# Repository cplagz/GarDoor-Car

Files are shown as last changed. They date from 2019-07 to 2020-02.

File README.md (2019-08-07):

# GarDoor-Car:
Version: 2.00R

## ESP8266 MQTT Garage Door Opener, Garage Door and Car Sensor, and Temperature Monitor using Home Assistant/Blynk
This project allows you to control (open/close) a "dumb" garage door opener for a garage door and independently reports the garage door status (open/closed) and presence of a car in the garage via MQTT and Blynk. In addition you can monitor the Temperature and Humidity within your garage over MQTT as well. This project requires two ultrasonic sensors: one pointed at the garage door, and the other pointed at the normal location of the car. This allows the presence of the car to be detected whether the garage door is open or closed.  

The code covered in this repository utilises Home Assistant's [MQTT Cover Component](https://www.home-assistant.io/components/cover.mqtt/), [MQTT Binary Sensor Component](https://www.home-assistant.io/components/binary_sensor.mqtt/), and [MQTT Sensor Component](https://www.home-assistant.io/components/sensor.mqtt/). There is an example configuration in this repository. GarDoor will respond to HA's open and close commands and reports door/car status to keep HA's GUI in sync with the door and car state. GarDoor should also be controllable via any home automation software that can work with MQTT.  

GarDoor can also be used with the Blynk app (iOS or Android). If you enable this feature, you can monitor the garage door/car status as well as open/close the door with the app. You can also choose to be notified of garage door events on your phone. 

GarDoor requires both hardware and software components. It requires an ESP8266 microcontroller with sensors and a relay. If you select the appropriate parts, you can build a GarDoor-Car device with no soldering! The software component is found in this repo. 

The code is based on DotNetDann's ESP-MQTT-GarageDoorSensor project (thanks Daniel) (which took inspiration from GarHAge and OpenGarage) with added additional features. Parts of the documentation is based on GarHAge documentation (thanks Mark).   

### Supported Features Include
- Reports status of the garage door
- Reports presence of a car in the garage whether the door is open or closed
- Reports ultrasonic sensors distance readings
- Reports information about the ESP8266
- Reports information on temperature and humidity
- Ability to select Celius or Fahrenheit for temperature
- Web page for status of the garage door, car presence, and temperature/humidity
- Ability to use the Blynk App (iOS or Android) to open/close the garage door and monitor door/car status
- Ability to receive Blynk notifications when garage door is opened/closed and when door is left open for more than 15 minutes
- Events and status sent via MQTT
- MQTT commands to toggle relay to open/close the garage door
- Ability to select an Active High or Active Low relay
- Over-the-Air (OTA) Upload from the ArduinoIDE!

### How GarDoor-Car Operates

GarDoor-Car subscribes to a configurable MQTT topic for the garage door (by default, gardoor/1/action).

When the OPEN payload is received on this topic, GarDoor-Car momentarily activates the relay connected to the garage door opener to cause the door to open.

When the CLOSE payload is received on this topic, GarDoor-Car momentarily activates the relay connected to the garage door opener to cause the door to close. By default, GarDoor-Car is configured to activate the same relay for the OPEN and CLOSE payloads, as most (if not all) garage door openers operate manually by momentarily closing the same circuit to both open and close.

When the STATE payload is received on this topic, GarDoor-Car publishes the status of the garage door (open or closed) to the topic gardoor/1/status and the occupied status of the car (true or false) to the topic gardoor/2/status. The distance measurements for the door and car sensors are also included in these messages. These messages are published with the "retain" flag set. To ensure that HA displays up-to-date garage door and car status after a HA restart, it is recommended that you create an automation in Home Assistant that publishes the STATE payload via MQTT on HA start. An example is provided in the Home Assistant Configuration section of this documentation.

When the state of the garage door changes (either because GarDoor-Car (via HA/MQTT or Blynk app) has triggered the door to open or close, or because the door has been opened or closed via a remote, pushbutton switch, key switch, or manually), GarDoor-Car publishes the status (open or closed) and sensor distance measurement of the garage door to gardoor/door/1/status. These messages are published with the "retain" flag set.

When the occupied state of the car changes because the car leaves or enters the garage, GarDoor-Car publishes the occupied status (true or false) and sensor distance measurement of the car to gardoor/2/status. These messages are published with the "retain" flag set.

GarDoor-Car also publishes (topic gardoor/availability) a "birth" message on connection to your MQTT broker, and a "last-will-and-testament" message on disconnection from the broker, so that your home automation software can respond appropriately to GarDoor-Car being online or offline.

GarDoor-Car also publishes to your MQTT broker on topic gardoor/blynkavailability (only if GarDoor-Car is already online; if GarDoor-Car goes offline first, then an automation in your home automation software is required to update the status on the gardoor/blynkavailability topic) a message when GarDoor-Car connects or disconnects from the Blynk server, so that your home automation software can respond appropriately to the GarDoor-Car Blynk connection being online or offline.

GarDoor-Car publishes data about the ESP8266 (topic gardoor/ESPtoMQTT) and temperature/humidity (topics gardoor/temperature and gardoor/humidity) to your MQTT broker.

GarDoor-Car can also connect (if enabled by the user) to a Blynk server. This enables door and car status updates, as well as the door sensor distance measurement to be published to a Blynk server/app. GarDoor-Car can also receieve button requests from the Blynk server/app, which causes GarDoor-Car to momentarily activate the relay connected to the garage door opener to cause the door to open or close. This feature gives a user the ability to press a button in the Blynk app to control the garage door. Notifications can also be published to the Blynk server/app when the garage door open/closes or is left open too long. 

### Hardware Parts List
- [NodeMCU](https://www.aliexpress.com/item/32665100123.html) or other ESP8266-based microcontroller 
- [2 x HC-SR04P Ultrasonic Sensors](https://www.aliexpress.com/item/32711959780.html) May also use HC-SR04 model
- [5V 1 Channel Relay Board](https://www.gearbest.com/relays/pp_226384.html) Active-High or Active-Low supported
- [DHT22 module](https://www.aliexpress.com/item/32899808141.html) (optional)  
- Electrical cable (two-conductor) to connect the relay to your garage door opener 
- Power source for NodeMCU: MicroUSB cable with USB 2.1A power adapter or 5V power supply  
- Male-to-female (and male-to-male if you use HC-SR04 model ultrasonic sensors and need to connect four components to 5v power using the breadboard power rails) breadboard jumper wires (Dupont)
- Breadboard 400 tie-point or larger
- Project box or case (optional)

#### Detailed Hardware

#### 1. ESP8266-based microcontroller
I recommend the NodeMCU as GarDoor-Car was developed and is tested on it. Its advantages are:

- it comes with header pins already soldered so that it can plug directly into a solderless breadboard;
- its VIN (or VU on the LoLin NodeMCU v3 variant) port can power the 5v relay module and DHT22 sensor;
- it can be powered and programmed via MicroUSB;
- it has Reset and Flash buttons, making programming easy.

This guide is written specifically for the NodeMCU. But, GarDoor-Car should also work with the Adafruit HUZZAH, Wemos D1, or similar, though you may need to adjust the GPIO ports used by the sketch to match the ESP8266 ports that your microcontroller makes available.

#### 2. Single 5v relay module
A single 5v relay module makes setup easy: just plug jumper wires from the module's VCC, S, and GND pins to the NodeMCU. Because the relay module is powered by 5v, its inputs can be triggered by the NodeMCU's GPIOs.

GarDoor-Car will work with relay modules that are active-high or active-low; if using an active-low relay, be sure to set the relevant configuration parameter in auth.h, described below, and test thoroughly to be sure that your garage door opener(s) are not inadvertently triggered after a momentary power-loss.

#### 3. Two Ultrasonic Sensors (model HC-SR04P recommended)
GarDoor-Car will work with either the HC-SR04 or HC-SR04P model. The HC-SR04P can use 3.3v or 5v power, while the HC-SR04 requires 5v power. When using the HC-SR04P model (as the wiring diagram below assumes), the maximum distance of the sensor is reduced slightly when using 3.3v power. For the purposes of this project, this shouldn't affect the results of the GarDoor-Car. Thus either model can be used, but it is recommended that you use the HC-SR04P powered using 3.3v.  

While a HC-SR04P works using 3.3v power without any other changes to the design (see the wiring diagram below), if using HC-SR04 sensors (which require you to connect them to the 5v VCC for power), a 1k Ω resistor will need to be used between the ECHO pin on each distance sensor and the related input pin on the NodeMCU. 

#### 4. 5v MicroUSB cable and power supply
Power your NodeMCU via the same type of power supply used to charge Android phones or power a RaspberryPi. Powering the NodeMCU via MicroUSB cable and power adapter is recommended since the relay module & DHT22 sensor can be powered via the NodeMCU VIN (or VU on the LoLin v3 variant) pin. A USB power adapter with 2.1A or above is recommended. 

#### 5. Solderless breadboard (400 tie-point or larger)
The NodeMCU may be mounted in the center of this breadboard nicely, leaving a female port next to each NodeMCU pin on both sides. However for this project it is important that the two ultrasonic sensors use the same trigger pin, and the relay and DHT22 sensor both use the 5v VIN power pin. 

To overcome this you could use male-to-male jumper wires. You would connect the 5v/ground and one set of 3.3v/ground NodeMCU pins to each set of outside power rails on the breadboard using male-to-male jumper wires. Then connect the male end of a male-to-female jumper wire for a relay/sensor's power and ground to a + (for power) or - (for ground) port on the appropriate 3.3V or 5V rail to provide power/ground to components using the rails.  

In the same way, you would connect the NodeMCU output to be used as the trigger (pin D5) to a port above the NodeMCU using a male-to-male jumper wire. Then you would connect the male end of the male-to-female jumper wires connected to the trig pin of each ultrasonic sensor, to two ports in the same line on the broadboard as the male end of the wire connected to pin D5 of the NodeMCU.  

You may also choose to mount the DHT22 and/or relay modules directly on the breadboard by inserting their pins vertically into ports above the NodeMCU. If do this you will require male-to-male jumper wires to connect the 3 ports of the DHT22 and 3 ports of the relay to the appropriate ports on the breadboard to link to the NodeMCU's pins.  

This makes for a clean and solderless installation. Finally, these breadboards often also have an adhesive backing, making mounting in your project box easy.

#### 6. A DHT22 module (optional)
This sensor provides temperature/humidity readings to GarDoor-Car, but is optional and can be disabled in the auth.h file. The module verion (which is mounted on a board) is recommended, since the board includes a pull-up resister to reduce the output to 3.3v (the DHT22 is powered using 5v). If you use a DHT22 sensor (without a module board), you will need to use a 10k Ω resistor wired to the power input and the data pin of the DHT22 to act as a pull-up.   

#### 7., 8., & 9. Miscellaneous parts
To install GarDoor-Car, you will also require:

- Low voltage/current two-conductor electrical wire of the appropriate length to make connections from the relay where GarDoor-Car is mounted to the garage door opener.
- Male-to-female breadboard jumper wires to make connections from the NodeMCU via the breadboard ports to the relay module (3 wires required), the DHT22 (3 wires required), and the two ultrasonic sensors (4 wires required for each). 
- You will also require male-to-male jumper wires to use the outside power rails (4 wires) and to connect both ultrasonic sensors trig pins to the same NodeMCU pin (1 wire). If you choose to insert the DHT22 or relay's pins vertically on the breadboard, you will need further male-to-male jumper wires (up to 6 wires) instead of male-to-female wires.   
- A project box to hold the NodeMCU, the relay module, the DHT22 sensor module (if required), and the two ultrasonic sensors. While the ultrasonic sensors can be mounted inside the same box as the nodeMCU, they will need to have unobstructed access outside the box to point at the garage door and car.  

### Building GarDoor-Car

See the wiring diagram below for an example of how the pins are wired up. 

- Attach your NodeMCU to the middle (between the outside power rails) of the solderless breadboard at one end; the MicroUSB connector should be facing one of the short outside edges of the breadboard (the power rails are on the longer outside edges). Ensure that there are at least two female ports next to each NodeMCU pin on each side of the NodeMCU.
- Mount the solderless breadboard in your project box.
- Mount the relay module in your project box. You could insert lengthways the relay's three pins into the breadboard above the position of the NodeMCU so that the relay stands up on top of the breadboard. If you do this then you will use male-to-male jumper wires plugged into ports on the breadboard to connect the relay's pins to the NodeMCU. 
- Mount the DHT22 module in your project box (if required). You could insert lengthways the DHT22's three pins into the breadboard above the position of the NodeMCU so that the DHT22 stands up on top of the breadboard. If you do this then you will use male-to-male jumper wires plugged into ports on the breadboard to connect the DHT22's pins to the NodeMCU.  
- Label your two HC-SR04P sensors as sensor 1 (door) and sensor 2 (car). Mount the two HC-SR04P sensors in your project box, ensuring there are holes for the front of the sensors to "see" the outside. Ensure that the direction you mount sensor 1 in will enable it to "see" the garage door once you position the box in its intended location in the garage. Also ensure that sensor 2 will be able to "see" the position of the car when the box is in the garage. You could mount the box above the garage floor or on the side of the garage wall.     
- Plug a m-to-m jumper wire from the VIN / VU port on the NodeMCU into the + power rail on one side of the breadboard.
- Plug a m-to-m jumper wire from the GND port (near the VIN / VU port) on the NodeMCU into the - power rail on one side of the breadboard. 
- Plug a m-to-m jumper wire from a 3.3v port on the NodeMCU into the + power rail on the other side of the breadboard.
- Plug a m-to-m jumper wire from the GND port (near the 3.3v port you have used) on the NodeMCU into the - power rail on the other side of the breadboard. 
- Plug a f-to-m jumper wire from VCC / + on the relay module to the 5v + power rail.
- Plug a f-to-m jumper wire from GND / - on the relay module to the 5v - power rail.
- Plug a f-to-m jumper wire from S on the relay module to port D6 on the NodeMCU (or Arduino/ESP8266 GPI012).
- Plug a f-to-m jumper wire from + on the DHT22 module to the 5v + power rail.
- Plug a f-to-m jumper wire from - on the DHT22 module to the 5v - power rail.
- Plug a f-to-m jumper wire from Data on the DHT22 module to D7 port on the NodeMCU (or Arduino/ESP8266 GPI013).
- Plug a m-to-m jumper wire from the D5 port (or Arduino/ESP8266 GPI014) of the NodeMCU into a port on a spare line above the NodeMCU on the breadboard. 
- Plug a f-to-m jumper wire from VCC on the HC-SR04P sensor 1 module to the 3.3v + power rail.
- Plug a f-to-m jumper wire from GND on the HC-SR04P sensor 1 module to the 3.3v - power rail.
- Plug a f-to-m jumper wire from Trig on the HC-SR04P sensor 1 module to a port on the same line as the other end of the wire connected to D5 of the NodeMCU is plugged into.
- Plug a f-to-m jumper wire from Echo on the HC-SR04P sensor 1 module to D2 port on the NodeMCU (or Arduino/ESP8266 GPI04).
- Plug a f-to-m jumper wire from VCC on the HC-SR04P sensor 2 module to the 3.3v + power rail.
- Plug a f-to-m jumper wire from GND on the HC-SR04P sensor 2 module to the 3.3v - power rail.
- Plug a f-to-m jumper wire from Trig on the HC-SR04P sensor 2 module to a port on the same line as the other end of the wire connected to D5 of the NodeMCU is plugged into.
- Plug a f-to-m jumper wire from Echo on the HC-SR04P sensor 2 module to D1 port on the NodeMCU (or Arduino/ESP8266 GPI05).

*Done!*

#### Wiring Diagram
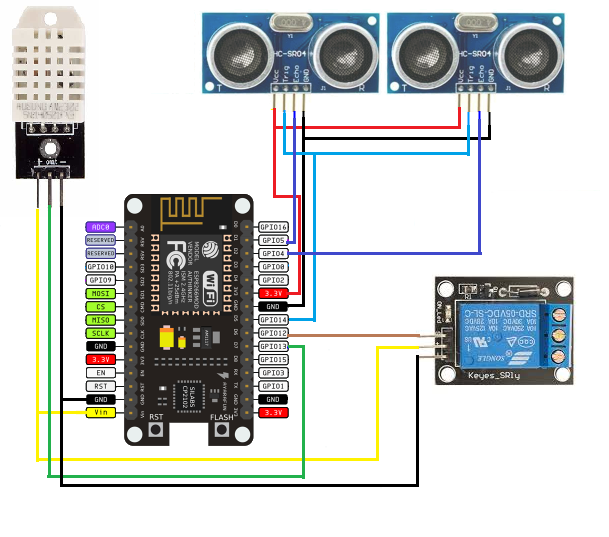
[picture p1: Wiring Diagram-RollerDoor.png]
Wiring Diagram


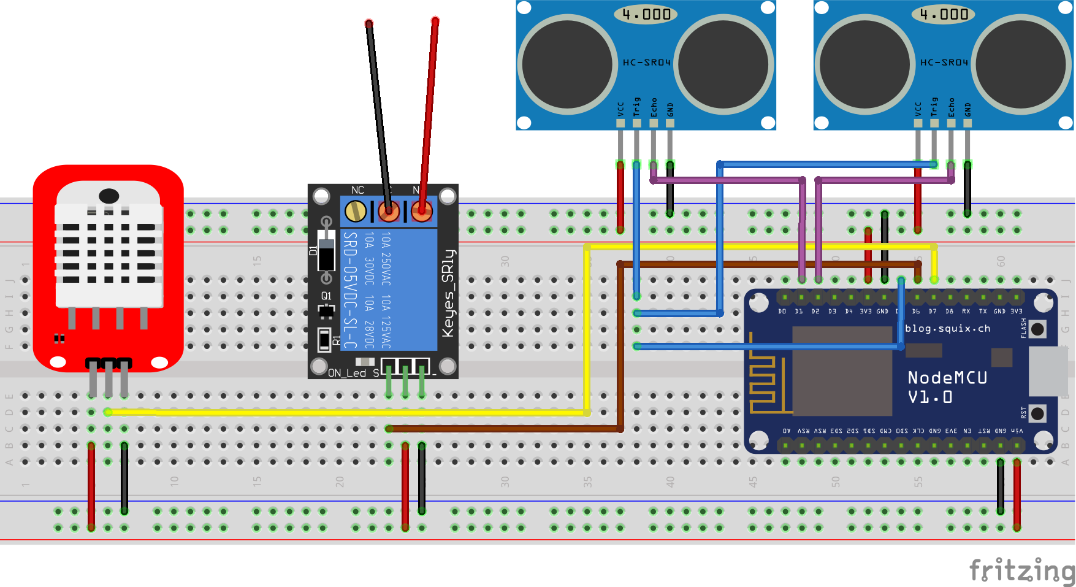
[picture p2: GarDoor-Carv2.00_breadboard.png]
Breadboard Diagram


### Software

#### 1. Set up the Arduino IDE

You will modify the configuration parameters and upload the sketch to the NodeMCU with the Arduino IDE.

1. Download the Arduino IDE for your platform from [here](https://www.arduino.cc/en/Main/Software) and install it.
2. Add support for the ESP8266 to the Arduino IDE by following the instructions under "Installing with Boards Manager" [here](https://github.com/esp8266/arduino).
3. Add the "PubSubClient", "NewPing", and "Blynk" libraries to the Arduino IDE: follow the instructions for using the Library Manager [here](https://www.arduino.cc/en/Guide/Libraries#toc3), and search for and install the PubSubClient, NewPing, and Blynk libraries.
4. You may need to install a driver for the NodeMCU for your OS - Google for instructions for your specific microcontroller and platform, install the driver if necessary, and restart the Arduino IDE.
5. Select your board from Tools - Boards in the Arduino IDE (e.g. "Generic ESP8266 Module").

#### 2. Install Blynk App and Project and get Token

- Install the Blynk app on your phone by finding the Blynk app in your app store ([Android](https://play.google.com/store/apps/details?id=cc.blynk&hl=en_US) and [Apple iOS](https://apps.apple.com/us/app/blynk-iot-for-arduino-esp32/id808760481) and installing it.
- Run the Blynk app, and create an account (if you don't already have one). 
- In the Blynk app find the menu option to scan a QR code, click it and then scan the QR code that’s located [here](https://github.com/OpenGarage/OpenGarage-Firmware/blob/master/OGBlynkApp/og_blynk_1.1.png) (OpenGarage Project for Blynk App). If you have just created a new Blynk account you will have enough energy credits to use the project in the app for free. If you already have other project(s) in your Blynk account, you may need to purchase further energy credits to use the OpenGarage project in the app.  
- Once the project is scanned, go to the Project Settings, and copy or email the Blynk authorisation token to yourself. This is the token you will need to put into the auth.h file in step 3 below.
- You can configure the project in the app, such as changing the name of the button, but DO NOT change the virtual pin numbers for any button or widget (V1, V2 etc).  

*NOTE: You can logon to the same Blynk account on more than one phone. If you do this on other family members phones, they can use the same project in the app to control the same GarDoor-Car.* 

#### 3. Load the sketch in the Arduino IDE and modify the user parameters in auth.h

Download the files from this repo to your computer, and open the GarDoor-Car-Vx.xx.ino file from the folder. GarDoor-Car's configuration parameters are found in auth.h. Select the auth.h tab in the Arduino IDE. This section describes the configuration settings and parameters and their permitted values. There are some settings that you must set, while others can be left as they are unless you have a specific reason to change them. 

If you wish to get up and running easily, these are the only settings you need to set:
- WIFI_SSID
- WIFI_PASSWORD
- MQTT_SERVER
- MQTT_USER and MQTT_PASSWORD (only if you use authentication on your MQTT Broker)
- MQTT_PORT (only if you use a non-default port)
- OTApassword (set your own password for this)
- BlynkAuthToken (unless you disable Blynk)
- ULTRASONIC_DIST_MAX_CLOSE
- ULTRASONIC_DIST_MAX_CAR
- RELAY_ACTIVE_TYPE
- DHT_ENABLED (if using a DHT22)
- DHT_TEMPERATURE_CELSIUS (if using a DHT22 and you wish to use the fahrenheit scale)

Important!! After making any desired changes save the auth.h file. 

*IMPORTANT: No modification of the sketch code in GarDoor-Car-Vx.xx.ino is necessary (or advised, unless you are confident you know what you are doing and are prepared for things to break unexpectedly).*

**Wifi Settings**

*NOTE: An available IPv4 network with a DHCP for IPv4 service is assumed* 

WIFI_HOSTNAME "your-device-name"

The wifi hostname GarDoor-Car will use. Should be unique among all the devices connected to your network. Must be placed within quotation marks. (Default: GarDoor)

WIFI_SSID "your-wifi-ssid"

The wifi ssid GarDoor-Car will connect to. Must be placed within quotation marks.

WIFI_PASSWORD "your-wifi-password"

The wifi ssid's password. Must be placed within quotation marks.

**MQTT Settings**

MQTT_SERVER "w.x.y.z"

The IPv4 address of your MQTT broker. Must be placed within quotation marks.

MQTT_USER "your-mqtt-username"

The username required to authenticate to your MQTT broker. Must be placed within quotation marks. Use "" (i.e. a pair of quotation marks) if your broker does not require authentication.

MQTT_PASSWORD "your-mqtt-password"

The password required to authenticate to your MQTT broker. Must be placed within quotation marks. Use "" (i.e. a pair of quotation marks) if your broker does not require authentication.

MQTT_PORT your-mqtt-server-port-number

The port on your MQTT server GarDoor-Car will use to connect to the MQTT service. Must be a number. (Default: 1883)

MQTT_AVAIL_TOPIC WIFI_HOSTNAME "mqtt-topic-for-gardoor-availability"

Name of the topic that the MQTT broker will host and HA will use to determine if GarDoor-Car is online or offline. Must be placed within quotation marks. (Default: /availability)

TimeReadSYS milliseconds

Number of milliseconds (1000 per second) between which system readings of ESP8266 data will be taken and published using MQTT. Must be a number. (Default: 100000)

topicESPtoMQTT WIFI_HOSTNAME "mqtt-topic-for-esp8266-data"

Name of the topic that the MQTT broker will host and HA will use to get running data about your ESP8266. Must be placed within quotation marks. (Default: /ESPtoMQTT)

**OTA Settings**

OTApassword "your-ota-password"

The password you will need to enter to upload remotely via the ArduinoIDE. Must be placed within quotation marks. (Default: ota password)

OTAport your-esp8266-device-port-number

The port you will need to enter into the ArduinoIDE to allow it to connect to your running ESP8266. Must be a number. (Default: 8266)

**Blynk App Settings**

BLYNK_ENABLED true

Set to true to allow you to use the Blynk app. Set to false to disable use of Blynk. (Default: true)

BlynkAuthToken "your-blynk-project-token"

The Blynk token from the project in the Blynk app (see step 2 above). Must be placed within quotation marks.  

BLYNK_NOTIFY true

Set to true to enable notifications via the Blynk app. Set to false to disable Blynk notifications. (Default: true)

BLYNK_DEFAULT_DOMAIN "blynk-server-address-or-name"

The name or IP address of the Blynk server the Blynk app/GarDoor-Car connects to. Only change this if you have setup a local Blynk server. Must be placed within quotation marks. (Default: blynk-cloud.com)  

BLYNK_DEFAULT_PORT blynk-server-port-number

The port the Blynk app/GarDoor-Car uses to connect to the Blynk server. Only change this if you have setup a local Blynk server. Must be a number. (Default: 80) 

BLYNK__AVAIL_TOPIC WIFI_HOSTNAME "mqtt-topic-for-blynk-availability"

Name of the topic that the MQTT broker will host and HA will use to determine if GarDoor-Car is connected to the Blynk server. Must be placed within quotation marks. (Default: /blynkavailability)

**Distance Parameters**

ULTRASONIC_MAX_DISTANCE number-in-cm

Maximum distance (in cm) to ping. If using HC-SR04P sensors should be 400. If using HC-SR04 sensors, should be 450. Must be a number. (Default: 400)  

ULTRASONIC_DIST_MAX_CLOSE number-in-cm

Maximum distance (in cm) to indicate that the garage door is closed (used by sensor 1). If the measured distance to the object is less than this, then the door is published as closed.If the measured distance to the object is more than this, then the door is published as open. Must be a number. (Default: 120)   

ULTRASONIC_DIST_MAX_CAR number-in-cm

Maximum distance (in cm) to indicate that the car is present (used by sensor 2). If the measured distance to the object is less than this, then the car is present. If the measured distance to the object is more than this, then the car is absent. Must be a number. (Default: 120)   

ULTRASONIC_SETTLE_TIMEOUT milliseconds 

Number of milliseconds (1000 per second) to wait between pings (as both sensors get triggered at the same time). Waiting between pings improves readings for each sensor. Must be a number. (Default: 500)

RELAY_ACTIVE_TIMEOUT milliseconds

Number of milliseconds (1000 per second) the relay will close to actuate the door opener.  While it is "closed" the NO connector on the relay will allow current to flow, while the NC connector will cut the flow of current. Must be a number. (Default: 500)

RELAY_ACTIVE_TYPE HIGH

Set to LOW if using an active-low relay module. Set to HIGH if using an active-high relay module. (Default: HIGH)

DOOR_TRIG_PIN 14

The ESP8266 GPIO pin that triggers the two ultrasonic sensors to determine the distance to an object and output the results on their Echo pins. Must be a number. (Default: 14) (which is D5 on the NodeMCU)

**Door 1 Parameters**

DOOR1_ALIAS "name"

The alias to be used for Door 1 (garage door) in serial messages, MQTT topic and webpage. Must be placed within quotation marks. (Default: Door)

MQTT_DOOR1_ACTION_TOPIC WIFI_HOSTNAME "mqtt-topic"

The MQTT broker topic GarDoor-Car will subscribe to for action commands for Door 1 (garage door). Must be placed within quotation marks. (Default: /1/action)

MQTT_DOOR1_STATUS_TOPIC WIFI_HOSTNAME "mqtt-topic"

The Mqtt broker topic GarDoor-Car will publish Door 1's (garage door) status to. Must be placed within quotation marks. (Default: /1/status)

DOOR1_RELAY_PIN 12

The ESP8266 GPIO pin connected to the relay signal pin which causes the relay to "close" allowing current to flow. The relay is in turn connected to the garage door opener's terminals, using either the NO (normally open) or NC (normally close) connector plus the common connector. This assumes that the same terminals control open and close via a momentary connection of the terminals, which most garage door opener's do. (Default: 12) (which is D6 on the NodeMCU)

DOOR1_ECHO_PIN 4

The ESP8266 GPIO pin that receives the echo pin output of sensor 1 to measure the distance from the sensor pointed towards the garage door. Must be a number. (Default: 4) (which is D2 on the NodeMCU)

DOOR1_LIMIT_RELAY_CLOSE

Set to true to prevent the relay from opening the garage door (only close will work). Set to false to be able to use the relay to both open and close the door. (Default: false)

**Car Parameters**

CAR_ALIAS "name"

The alias to be used for the car in serial messages, MQTT topic and webpage. Must be placed within quotation marks. (Default: Car)

MQTT_CAR_STATUS_TOPIC WIFI_HOSTNAME "mqtt-topic"

The Mqtt broker topic GarDoor-Car will publish the Car's occupied status to. Must be placed within quotation marks. (Default: /2/status)

DOOR1_ECHO_PIN 5

The ESP8266 GPIO pin that receives the echo pin output of sensor 2 to measure the distance from the sensor pointed towards the car's normal location. Must be a number. (Default: 5) (which is D1 on the NodeMCU)

**DHT Parameters**

DHT_ENABLED true

Set to true if you include a DHT sensor in your hardware. Set to false to disable the use of a DHT sensor. (Default: true)

DHT_PIN 13 // D7 on ESP8266

The ESP8266 GPIO pin that receives the output of the DHT sensor to measure temperature and humidity. Must be a number. (Default: 13) (which is D7 on the NodeMCU)

DHT_TYPE DHT22 

Set to DHT22 (for DHT22 / AM2302 / AM2321) or DHT21 (for DHT21 / AM2301) or DHT11 depending on the type of sensor you use. (Default: DHT22)

MQTT_TEMPERATURE_TOPIC WIFI_HOSTNAME "mqtt-topic"

The Mqtt broker topic GarDoor-Car will publish the DHT temperature readings to. Must be placed within quotation marks. (Default: /temperature)

MQTT_HUMIDITY_TOPIC WIFI_HOSTNAME "mqtt-topic"

The Mqtt broker topic GarDoor-Car will publish the DHT humidity readings to. Must be placed within quotation marks. (Default: /humidity)

DHT_PUBLISH_INTERVAL seconds 

Number of seconds between between each temperature/humidity reading that will be taken and published using MQTT. Must be a number. (Default: 300)

DHT_TEMPERATURE_CELSIUS true

Set to true if you wish temperature to be reported using celsius scale, or false to report temperature using fahrenheit scale. (Default: true)

DHT_TEMPERATURE_ALIAS "name"  

The alias to be used for the temperature output in serial messages, MQTT topic and webpage. Must be placed within quotation marks. (Default: Garage Temperature)

DHT_HUMIDITY_ALIAS "name"
 
The alias to be used for the humidity output in serial messages, MQTT topic and webpage. Must be placed within quotation marks. (Default: Garage Humidity)

#### 4. Upload the sketch to your NodeMCU / microcontroller

Ensure that the Auduino IDE is running and the sketch is loaded and configured. If using the NodeMCU, connect it to your computer via MicroUSB. The NodeMCU will connect to a virtual COM port within the Auduino IDE.   

Configure the Arduino IDE for the upload using the settings shown in the figure below:  

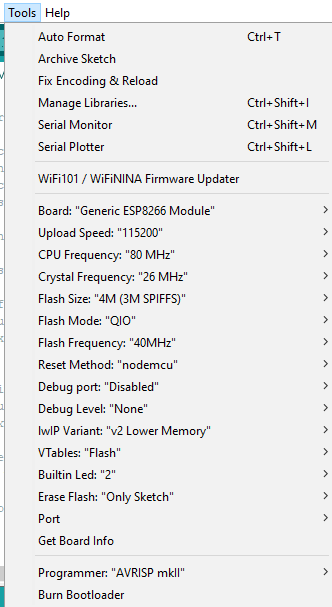
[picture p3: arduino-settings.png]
Arduino IDE Settings


There are two uploads methods you can use:
- In the Arduino IDE, Tools - Ports menu ensure that the COM port is selected that the NodeMCU is connected to. Also ensure you have configured the settings for the Generic ESP8266 Board as shown in the figure above. Then select Sketch - Upload. 
- Press and hold the reset button on the NodeMCU, press and hold the Flash button on the NodeMCU, then release the Reset button. Select Sketch - Upload in the Arduino IDE.

If using a different ESP8266 microcontroller, follow that device's instructions for putting it into flashing/programming mode.

#### 5. Check the Arduino IDE Serial Monitor

Open the Serial Monitor via Tools - Serial Monitor. Reset your microcontroller. If all is working correctly, you should see something similar to the following messages:

```
Starting GarDoor-Car...

Connecting to your-wifi-ssid.. WiFi connected - IP address: 192.168.1.100
Attempting MQTT connection...Connected
Publishing birth message "online" to GarDoor/availability...
Attempting BLYNK connection...Connected!
Publishing message "blynkon" to GarDoor/blynkavailability...
Subscribing to GarDoor/1/action...
Door closed! Publishing to GarDoor/1/status...
Car Absent! Publishing to GarDoor/2/status...
```

If you receive these (or similar) messages, all appears to be working correctly. 

#### 6. Check Blynk App

Make sure the Blynk project is running (in the project there is a triangle-shaped Run button). You should get a distance reading in the app and be able to click the button to activate the relay. 

#### 7. Reserve an IPv4 address on your DHCP service

Logon onto your router (or device/server) that runs your DHCP service. Reserve the IP address of the GarDoor-Car device (also known as a DHCP static binding). This ensures that GarDoor-Car always uses the same IP address when it reboots. This makes it easier to open the webpage or upload a new sketch using Arduino OTA.  

Disconnect GarDoor-Car from your computer and prepare to install it in your garage.

### Installing GarDoor-Car in your Garage

- Mount GarDoor-Car in your garage (above the garage floor or on a wall).
- Point Sensor 1 at the garage door and secure the position of the sensor.
- Point Sensor 2 at the normal location of the car in the garage and secure the position of the sensor. 
- Connect two-conductor voltage wire to the NO (or NC if that suits your opener) and COMMON terminals of your relay module;          run the wire to the garage door opener for the door and connect to the opener's terminals (the same terminals that the pushbutton or key switch for your door is attached to). Two of the opener's terminals connected to a wall switch or key switch or pushbutton are the ones you need to connect the relay to. You can determine which ones they are, by using a single wire and shorting two of the terminals at a time until the door opens/closes. Once you have identified the two terminals you need to connect to, connect a wire to each one. The other end of one of the wires goes to the COMMON terminal on the relay, and the other end of the second wire connects to the NO (normally open) terminal.
- Plug the MicroUSB cable into a USB power supply (2.1A or above). 

*Done!*
    
### Home Assistant Configuration 

GarDoor-Car supports Home Assistant's "MQTT Cover", "MQTT Binary Sensor", and "MQTT Sensor" platforms.

HA configuration examples are shown in the yaml file in this repo (click the link below). 

[YAML Configuration](https://github.com/SmbKiwi/GarDoor-Car/blob/v2.00R/Example%20Home%20Assistant%20Configuration.yaml)

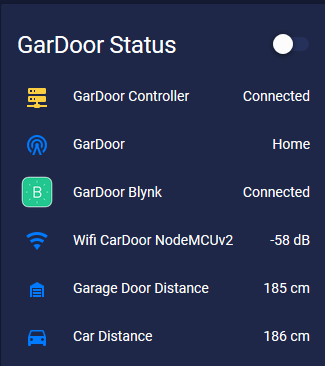
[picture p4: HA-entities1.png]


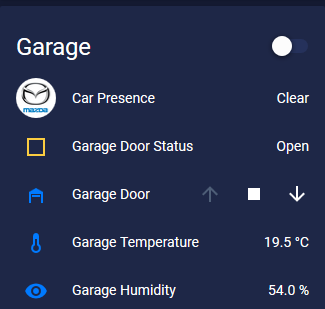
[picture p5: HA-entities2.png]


A status update from GarDoor-Car can be triggered by pressing the stop button (shown in the figure above) for the door in the HA GUI. 

### Blynk App

If you enabled Blynk, on your smartphone run the Blynk app and click the triangle-shaped Run button to make sure the Blynk project is running. You can now monitor the status of the door/car and open/close your garage door. If you left Blynk notifications enabled in the auth.h file, you will receive notifications when the garage door is opened or closed, and every 15 minutes when the door is left open.   



### Ariela App Notifications

If you use the Ariela App, you can configure HA to send notifications about the garage door to the app. Click the link below to learn how to set this up. 

[Ariela Push Notifications](http://ariela.surodev.com/2019/05/08/push-notifications-2/)

### Web page Examples

In a browser, enter the IP address w.x.y.z of the GarDoor-Car in the address bar. You can monitor the garage door, car, temperature, humidity and view some of the settings (see the figures below). 

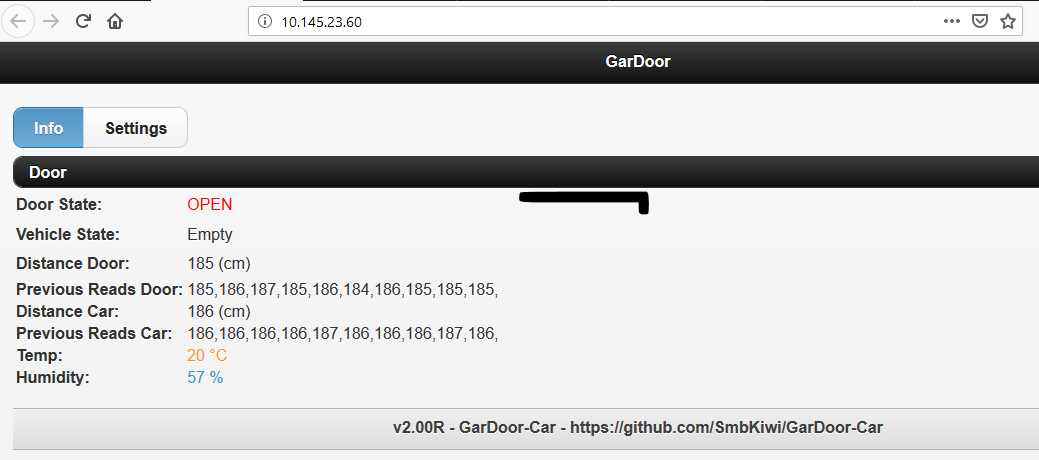
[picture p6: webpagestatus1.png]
Webpage Status


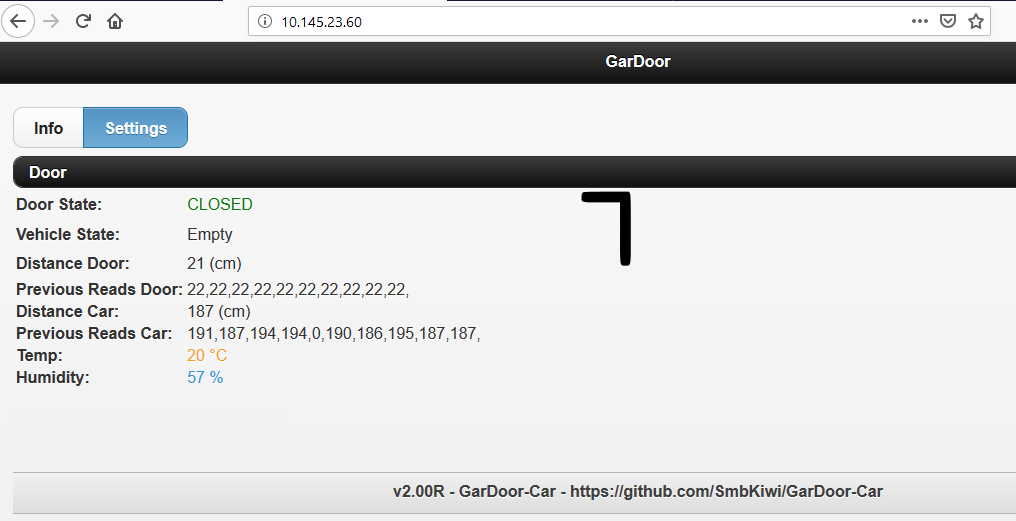
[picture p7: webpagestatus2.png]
Webpage Status


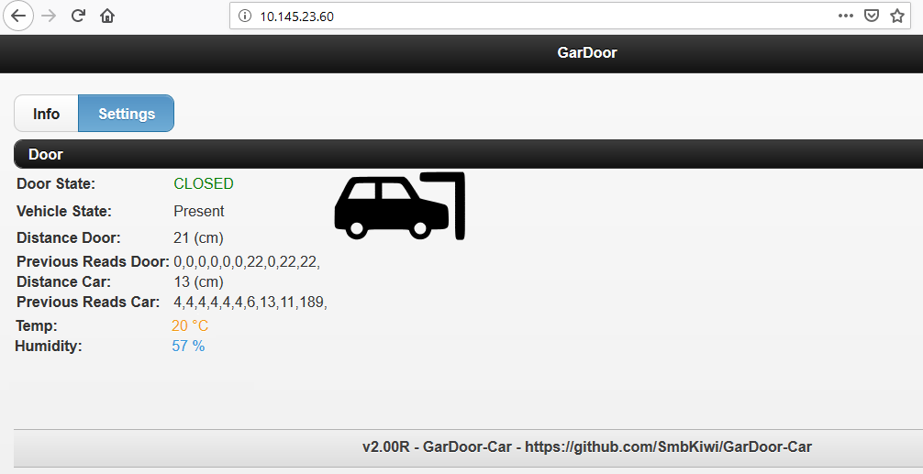
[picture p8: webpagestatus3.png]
Webpage Status


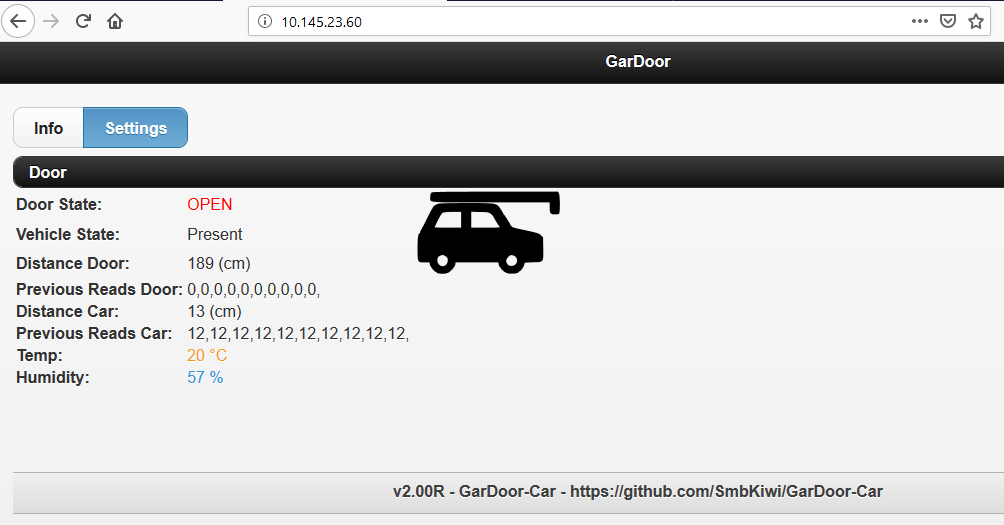
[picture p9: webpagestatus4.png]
Webpage Status


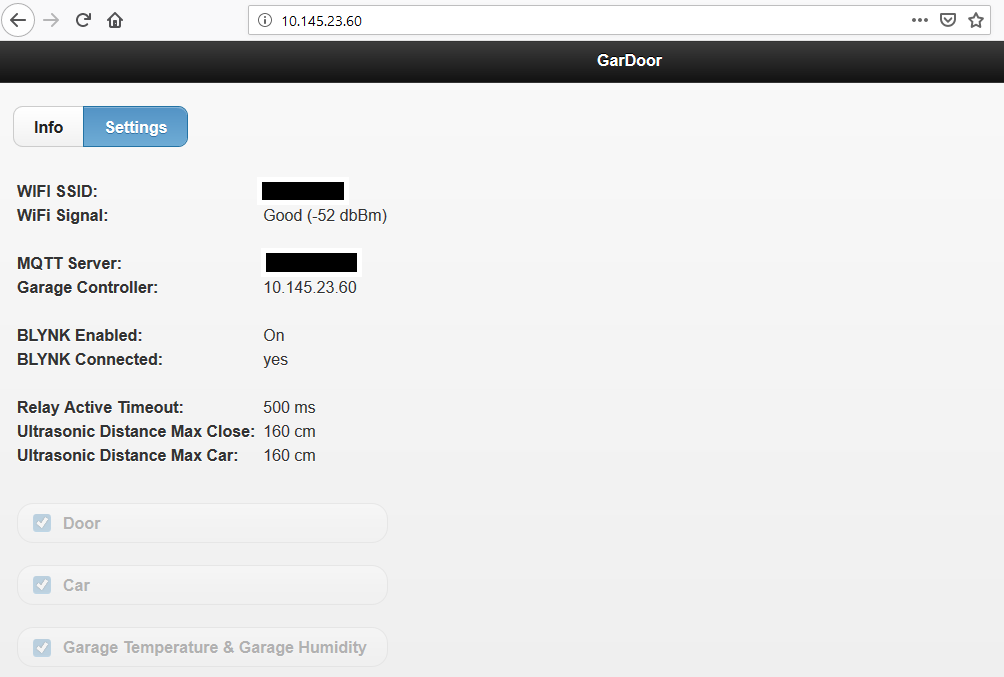
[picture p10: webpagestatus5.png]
Webpage Status


#### Sample MQTT commands

Listen to MQTT commands
> mosquitto_sub -h 172.17.0.1 -t '#'

Open the garage door
> mosquitto_pub -h 172.17.0.1 -t GarDoor/1/action -m "OPEN"

#### OTA Uploading

This code also supports remote uploading to the ESP8266 using Arduino's OTA library. To utilise this, you'll need to first upload the sketch using the traditional USB method. However, if you need to update your code after that, your WIFI-connected ESP chip should show up in Arduino IDE as an option under Tools -> Port -> 'HostName'at your.ip.address.xxx. 

More information on OTA uploading can be found [here](http://esp8266.github.io/Arduino/versions/2.0.0/doc/ota_updates/ota_updates.html).

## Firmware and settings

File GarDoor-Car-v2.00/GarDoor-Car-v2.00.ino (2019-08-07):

/*
  GarDoor-Car:
  
  This project allows you to control (open/close) a "dumb" garage door opener for a garage door and independently report the garage door status (open/closed) and presence of a car in the garage via MQTT. 
  In addition you can monitor the Temperature and Humidity within your garage over MQTT as well. 
  This project requires two ultrasonic sensors: one pointed at the garage door, and the other pointed at the normal location of the car. 
  This allows the presence of the car to be detected whether the garage door is open or closed.

  The code includes implementation of a webpage, MQTT, and Blynk. It requires an ESP8266 microcontroller with sensors and a relay. 
  
  To use this code you will need the following dependencies:

  - Support for the ESP8266 boards.
      - You can add it to the board manager by going to File -> Preference and pasting http://arduino.esp8266.com/stable/package_esp8266com_index.json into the Additional Board Managers URL field.
      - Next, download the ESP8266 dependencies by going to Tools -> Board -> Board Manager and searching for ESP8266 and installing it.

  - You will also need to download the following libraries by going to Sketch -> Include Libraries -> Manage Libraries
      - NewPing
      - PubSubClient     
      - Blynk

   This project is based on DotNetDann's ESP-MQTT-GarageDoorSensor, but has been modified and expanded by SmbKiwi. 
   This code was forked from https://github.com/DotNetDann/ESP-MQTT-GarageDoorSensor

   Inspiration for the addition of Blynk came from the OpenGarage project.

   - Another like project https://hackaday.io/project/25090/instructions

   Copyright (c) 2019 SmbKiwi 
  
   Licensed under the Apache License, Version 2.0 (the "License");
   you may not use this file except in compliance with the License.
   You may obtain a copy of the License at

       http://www.apache.org/licenses/LICENSE-2.0

   Unless required by applicable law or agreed to in writing, software
   distributed under the License is distributed on an "AS IS" BASIS,
   WITHOUT WARRANTIES OR CONDITIONS OF ANY KIND, either express or implied.
   See the License for the specific language governing permissions and
   limitations under the License.  
*/

//(Developer: SmbKiwi)
//2.00R Add support for Blynk App (you can use the QR code for OpenGarage project for Blynk App). Added MQTT publishing of ESP8266 data, ability to set relay type, and other small changes 
//1.10R Design for a single garage door with seperate car detection using 2 ultrasonic sensors 

//(Developer: DotNetDann)
// 1.8 Change pins and small clean
// 1.7 Add ability to only close garage doors
// 1.6 Add diagnose infomation on distances
// 1.4 Changes to use NewPing
// 1.3 adds DHT Sensor for Temp and Humidty  

// ------------------------------
// ---- all config in auth.h ----
// ------------------------------
#define VERSION F("v2.00R - GarDoor-Car - https://github.com/SmbKiwi/GarDoor-Car ")

#include <BlynkSimpleEsp8266.h> // Volodymyr Shymanskyy
#include <ArduinoJson.h> // Benoit Blanchon
#include <ESP8266WiFi.h>
#include <ESP8266WebServer.h>
#include <ESP8266HTTPClient.h>
#include <PubSubClient.h> // Nick O'Leary
#include <NewPing.h> // Tim Eckel
#include <ArduinoOTA.h>
#include <DHT.h> // Adafruit
#include <Adafruit_Sensor.h> // Adafruit Unified Sensor
#include "auth.h"

#define DOOR_UNKNOWN         0x00
#define DOOR_OPENED          0x01
#define DOOR_CLOSED          0x02
#define CAR_NO               0x03
#define CAR_YES              0x04
#define CAR_UNKNOWN          0x05
#define DOOR_OPENEDNOCAR     0x06
#define DOOR_CLOSEDWITHCAR   0x07
#define DOOR_CLOSEDNOCAR     0x08
#define DOOR_OPENEDWITHCAR   0x09
#define NOTKNOWN             0x10
#define SONAR_NUM 2      // Number of sensors required

/**************************************** GLOBALS ***************************************/

char* blynkup = "no"; // For displaying Blynk connection status in webpage
char auth[] = BlynkAuthToken;
bool curr_cloud_access_en() {
    if((unsigned)strlen(auth)==32) {
      return true;
    }
    return false;
  }
//if Blynk is enabled then initialise
#if BLYNK_ENABLED == true
  BlynkTimer timer;
  #define BLYNK_PIN_DOOR  V0
  #define BLYNK_PIN_RELAY V1
  #define BLYNK_PIN_LCD   V2
  #define BLYNK_PIN_DIST  V3
  #define BLYNK_PIN_CAR   V4
  #define BLYNK_PIN_IP    V5
  WidgetLED blynk_door(BLYNK_PIN_DOOR);
  WidgetLED blynk_car(BLYNK_PIN_CAR);
  char bdomain[] = BLYNK_DEFAULT_DOMAIN;
  uint16_t bport = BLYNK_DEFAULT_PORT;
  char* blynkonMess = "blynkon";  // MQTT topic Blynk is availiable
  char* blynkoffMess = "blynkoff";  //MQTT topic Blynk is not availiable  
#endif

int lastdoor1state = 2;  // Last state of door is unknown (used for Blynk notification when garage door is still open)
unsigned long timeropendoor = 0; // Time that garage door was first opened (used for Blynk notification when garage door is still open)
int n_opendoor = 1; // How many 15 minute periods the garage door has been continuously open for

const int BUFFER_SIZE = JSON_OBJECT_SIZE(10);
#define MQTT_MAX_PACKET_SIZE 512
unsigned long timersysdata = 0;

const int door_numValues = 10;
int door1_lastDistanceValues[door_numValues];
int door2_lastDistanceValues[door_numValues];
int door1_lastDistanceValue = 0;
int door2_lastDistanceValue = 0;

char* birthMessage = "online";
const char* lwtMessage = "offline";

const unsigned long dht_publish_interval_s = DHT_PUBLISH_INTERVAL;
unsigned long dht_lastReadTime = -1000;

const char* mqtt_broker = MQTT_SERVER;
const char* mqtt_clientId = WIFI_HOSTNAME;
const char* mqtt_username = MQTT_USER;
const char* mqtt_password = MQTT_PASSWORD;
String availabilityBase = WIFI_HOSTNAME;
String availabilitySuffix = "/availability";
String availabilityTopicStr = availabilityBase + availabilitySuffix;
const char* availabilityTopic = availabilityTopicStr.c_str();

// Set type of relay for turning relay on/off
#if RELAY_ACTIVE_TYPE == HIGH
  #define RELAYACTIVE HIGH
  #define RELAYINACTIVE LOW  
#endif
#if RELAY_ACTIVE_TYPE == LOW
  #define RELAYACTIVE LOW
  #define RELAYINACTIVE HIGH    
#endif

/******************************** GLOBAL OBJECTS *******************************/

NewPing sonar[SONAR_NUM] = {   // Sensor object array.
  NewPing(DOOR_TRIG_PIN, DOOR1_ECHO_PIN, ULTRASONIC_MAX_DISTANCE), // Each sensor's trigger pin, echo pin, and max distance to ping. 0-2
  NewPing(DOOR_TRIG_PIN, DOOR2_ECHO_PIN, ULTRASONIC_MAX_DISTANCE)  
};

WiFiClient espClient;
PubSubClient client(espClient);
ESP8266WebServer server(80);
DHT dht(DHT_PIN, DHT_TYPE);

// Get the state of the garage door based upon the sensor distance
byte getStateDoor(int distance1)
{
  if (distance1 <= 1) {
    garagestillopen(2);
    return DOOR_UNKNOWN; // Should not ever be this close. Probably an error
  } else if (distance1 <= ULTRASONIC_DIST_MAX_CLOSE) {
    garagestillopen(0);
    return DOOR_CLOSED;
  } else {
    garagestillopen(1);
    return DOOR_OPENED;   
  }
}

// determine how long door has been open and if so generate Blynk app message at 15 minute intervals until closed
void garagestillopen(int currdoorstate) {
  byte bnote = BLYNK_NOTIFY;
  if(BLYNK_ENABLED && curr_cloud_access_en && bnote) {  //if Blynk not in use then don't do anything
    if (currdoorstate == 2) lastdoor1state = 2;  // Door is unknown
    else if (currdoorstate == 0) lastdoor1state = 0;  // Door is closed 
    else if (currdoorstate == 1){  // Check door is open
      if (lastdoor1state == 0 || lastdoor1state == 2){   //This is the first time door is open
        timeropendoor = millis();  // record time door was first open
        lastdoor1state = 1;  //Door is now open
      } else if (lastdoor1state == 1){   //Door was open last time
          unsigned long currtime = millis();
          if (currtime > (timeropendoor + (n_opendoor * 15000 * 60))) {  //if door has been open at least 15 minutes
            String garmess = "Garage door has been open for ";
            int openmins = (n_opendoor * 15); 
            char* minsmess = "";
            itoa(openmins, minsmess, 10);
            String endmess = " minutes";
            String doornotify = "";
            doornotify = garmess + minsmess + endmess;  // put the message together
            #if BLYNK_ENABLED == true
            perform_notify(doornotify); // notify via Blynk app how many minutes door has been open
            #endif
            n_opendoor = n_opendoor + 1;  // increment to check for a further 15 minute later next time
          }                 
        }
    }  
  }
}

// Get the state of the car based upon the sensor distance
byte getStateCar(int distance2)
{
  if (distance2 <= 1) {
    return CAR_UNKNOWN; // Should not ever be this close. Probably an error
  } else if (distance2 <= ULTRASONIC_DIST_MAX_CAR) {
    return CAR_YES;
  } else {
    return CAR_NO;
  }
}

#include "web.h"

/********************************** START SETUP *****************************************/
void setup() {
  pinMode(LED_BUILTIN, OUTPUT);       // Initialize the LED_BUILTIN pin as an output (So it doesnt float as a LED is on this pin)
  digitalWrite(LED_BUILTIN, LOW);     // Turn the status LED on

  Serial.begin(115200);
  delay(10);
  Serial.println(F("Starting..."));

  // Setup Door 1 pins
  pinMode(DOOR1_RELAY_PIN, OUTPUT);
  digitalWrite(DOOR1_RELAY_PIN, RELAYINACTIVE);  // Turn off relay

  #if DHT_ENABLED == true
    dht.begin();
  #endif

  setup_wifi();

  client.setServer(mqtt_broker, MQTT_PORT);
  client.setCallback(callback);

  server.on("/", ServeWebClients);
  server.begin();

  #if BLYNK_ENABLED == true
  // If Blynk is enabled and has a valid token, then connect to Blynk server 
    if(curr_cloud_access_en) {
        Blynk.config(auth, bdomain, bport); // use the config function 
        Blynk.connect();
        while (Blynk.connect() == false) {Publish(BLYNK__AVAIL_TOPIC, blynkoffMess); }   // Wait until connected
        timer.setInterval(800L, reconnectBlynk);  // check every minute if still connected to server
        Serial.print(F("Blynk Connected"));
        Publish(BLYNK__AVAIL_TOPIC, blynkonMess);       
    }
  #endif
  
  //OTA SETUP
  ArduinoOTA.setPort(OTAport);
  ArduinoOTA.setHostname(WIFI_HOSTNAME); // Hostname defaults to esp8266-[ChipID]
  ArduinoOTA.setPassword((const char *)OTApassword); // No authentication by default

  ArduinoOTA.onStart([]() {
    Serial.println("Starting");
  });
  ArduinoOTA.onEnd([]() {
    Serial.println("\nEnd");
  });
  ArduinoOTA.onProgress([](unsigned int progress, unsigned int total) {
    Serial.printf("Progress: %u%%\r", (progress / (total / 100)));
  });
  ArduinoOTA.onError([](ota_error_t error) {
    Serial.printf("Error[%u]: ", error);
    if (error == OTA_AUTH_ERROR) Serial.println("Auth Failed");
    else if (error == OTA_BEGIN_ERROR) Serial.println("Begin Failed");
    else if (error == OTA_CONNECT_ERROR) Serial.println("Connect Failed");
    else if (error == OTA_RECEIVE_ERROR) Serial.println("Receive Failed");
    else if (error == OTA_END_ERROR) Serial.println("End Failed");
  });
  ArduinoOTA.begin();

  Serial.println(F("Ready"));
  digitalWrite(LED_BUILTIN, HIGH);     // Turn the status LED off
}


/********************************** START SETUP WIFI *****************************************/
void setup_wifi() {
  delay(10);
  Serial.print(F("Connecting to SSID: "));
  Serial.println(WIFI_SSID);

  // We start by connecting to a WiFi network
  WiFi.mode(WIFI_STA);
  //wifi_set_sleep_type(LIGHT_SLEEP_T); // Enable light sleep
  WiFi.hostname(WIFI_HOSTNAME);

  if (WiFi.status() != WL_CONNECTED) {  // FIX FOR USING 2.3.0 CORE (only .begin if not connected)
    WiFi.begin(WIFI_SSID, WIFI_PASSWORD);
  }

  while (WiFi.status() != WL_CONNECTED) {
    delay(500);
    Serial.print(F("."));
  }

  Serial.println(F(""));
  Serial.println(F("WiFi connected"));
  Serial.print(F("IP address: "));
  Serial.println(WiFi.localIP());
}

// Find out what the IP address is for the ESP8266
String get_ip() {
  String ip = "";
  IPAddress _ip = WiFi.localIP();
  ip = _ip[0];
  ip += ".";
  ip += _ip[1];
  ip += ".";
  ip += _ip[2];
  ip += ".";
  ip += _ip[3];
  return ip;
}

/********************************** START ESP8266 DATA *****************************************/
void getESPdata(){
    unsigned long currtime = millis();
    if (currtime > (timersysdata + TimeReadSYS)) { //If required period has passed since last read of data then read ESP data again
      timersysdata = millis();
      StaticJsonBuffer<MQTT_MAX_PACKET_SIZE> jsonBuff;
      JsonObject& ESPdata = jsonBuff.createObject();        
      unsigned long uptime = millis()/1000;      
      ESPdata["uptime"] = uptime;
      uint32_t freemem;
      freemem = ESP.getFreeHeap();
      ESPdata["freeMem"] = freemem;
      long rssi = WiFi.RSSI();
      ESPdata["rssi"] = rssi;
      String SSID = WiFi.SSID();
      ESPdata["SSID"] = SSID;             
      char JSONmessageBuffer[100];
      ESPdata.printTo(JSONmessageBuffer, sizeof(JSONmessageBuffer));  //put all JSON formatted ESP data into a variable 
      Publish(topicESPtoMQTT,JSONmessageBuffer); //publish ESP data from variable to MQTT topic
    }
}


/********************************** START CALLBACK *****************************************/
void callback(char* topic, byte* payload, unsigned int length) {
  Serial.println(F(""));
  Serial.print(F("Message arrived ["));
  Serial.print(topic);
  Serial.print(F("] "));

  for (int i = 0; i < length; i++) {
    Serial.print((char)payload[i]);
  }
  Serial.println();

  String topicToProcess = topic;
  payload[length] = '\0';
  String payloadToProcess = (char*)payload;

  // Action Command
  if (payloadToProcess == "OPEN") {
    Serial.print(F("Triggering OPEN relay!"));

    if (topicToProcess == MQTT_DOOR1_ACTION_TOPIC && // Door 1
         (getStateDoor(door1_lastDistanceValue) == DOOR_CLOSED) && // Garage is currently closed
         door1_lastDistanceValues[0] > 0 && // Last value was valid (Known state)
         !DOOR1_LIMIT_RELAY_CLOSE) { // We are not limiting the open command
      toggleRelay(DOOR1_RELAY_PIN);
      Serial.print(F("Door1 relay OPEN!"));   
    } else {
      Serial.print(F("criteria not meet!"));
    }
    
    Serial.println(" -> DONE");
  }
  else if (payloadToProcess == "CLOSE") {
    Serial.print(F("Triggering CLOSE relay!"));
    
    if (topicToProcess == MQTT_DOOR1_ACTION_TOPIC && 
         getStateDoor(door1_lastDistanceValue) == DOOR_OPENED &&  // Garage is currently OPEN
         door1_lastDistanceValues[0] > 0) { // Last value was valid (Known state)
      toggleRelay(DOOR1_RELAY_PIN);
      Serial.print(F("Door1 relay CLOSED!"));
    } else {
      Serial.print(F("criteria not meet!"));
    }

    Serial.println(F(" -> DONE"));
  }
  else if (payloadToProcess == "STATE") {
    Serial.print(F("Publishing on-demand status update!"));
    Publish(MQTT_AVAIL_TOPIC, birthMessage);
    sendState(1);
    sendState(2);
    Serial.println(F(" -> DONE"));
  }
  else if (payloadToProcess == "STOP") {
    Serial.print(F("We don’t know status of door while moving!"));
  } else {
    Serial.println(F("Unknown command!"));
  }
}


/********************************** START SEND STATE *****************************************/
void sendState(int door) {
  //Example JSON output on MQTT state topics
  //{"state":"open","occupied":unknown,"distance":12,"name":"Door1"}
  //{"state":"unknown","occupied":true,"distance":1000,"name":"Car"}
 
  StaticJsonBuffer<BUFFER_SIZE> jsonBuffer;
  JsonObject& root = jsonBuffer.createObject();

  // Determine state of door or car based on distance and buffer name and distance for MQTT topic
  byte statedoor = DOOR_UNKNOWN;
  byte statecar = CAR_UNKNOWN;  
  char* topic = "";
  if (door == 1) {
    statedoor = getStateDoor(door1_lastDistanceValue);
    topic = MQTT_DOOR1_STATUS_TOPIC;
    root["name"] = DOOR1_ALIAS;
    root["distance"] = door1_lastDistanceValue;
  } else if (door == 2) {
    statecar = getStateCar(door2_lastDistanceValue);
    topic = MQTT_CAR_STATUS_TOPIC;
    root["name"] = CAR_ALIAS;
    root["distance"] = door2_lastDistanceValue;
  } else {
    return;
  }

  //using state of door setup variables/buffer for MQTT topic and Blynk
  char* doorState = "unknown";  
  int door_status = 0; 
  if (statedoor == DOOR_OPENED) {
    doorState = "open";
    door_status = 1;
  } else if (statedoor == DOOR_CLOSED) {
    doorState = "closed";
  } else if (statedoor == DOOR_UNKNOWN) {
    doorState = "unknown";
  } 
//using state of car setup variables/buffer for MQTT topic and Blynk 
  char* occupiedState = "unknown";
  int vehicle_status = 0;
  if (statecar == CAR_YES) {
    occupiedState = "true";
    vehicle_status = 1;
  } else if (statecar == CAR_NO) {
    occupiedState = "false";
  } else if (statecar == CAR_UNKNOWN) {
    occupiedState = "unknown";    
  }
  
  root["state"] = doorState;
  root["occupied"] = occupiedState;

  char buffer[root.measureLength() + 1];
  root.printTo(buffer, sizeof(buffer));

  Publish(topic, buffer);  //Publish JSON data from buffer to MQTT topic

  // For HA. If you wish to use simple state result instead of JSON data
  if (door == 1) {
    char* extraTopicState = "/value";
    char extraTopic[100];
    snprintf(extraTopic, sizeof extraTopic, "%s%s", topic, extraTopicState);
    Publish(extraTopic, doorState);
  } else if (door == 2) {
      char* extraTopicState = "/value";
      char extraTopic[100];
      snprintf(extraTopic, sizeof extraTopic, "%s%s", topic, extraTopicState);
      Publish(extraTopic, occupiedState);
  }

  //send notification via Blynk App when garage door is opened or closed
  #if BLYNK_ENABLED == true
    static byte old_door_status = 0xff; 
    byte bnote = BLYNK_NOTIFY;
    char* compareState = "unknown";
    if(curr_cloud_access_en && bnote && (doorState != compareState)) {  //check if Blynk has valid token and notification is on, and if door is either closed or open
      if(door_status != old_door_status){  //check if door status has changed
        Serial.println(F(" Notify Blynk with text notification"));
        String garmess = "Garage door is currently ";
        String doormess = doorState;
        String doornotify = "";
        doornotify = garmess + doormess;  //Put the message together
        perform_notify(doornotify);
      }     
    }
  
  
    // Update door status, car status, door distance, and IP address to Blynk App
    if(Blynk.connected()) {
      Serial.println(F(" Update Blynk (State Refresh)"));  
      static String old_ip = "";      
      static byte old_vehicle_status = 0xff;
      static uint old_distance = 0;           
      if(door1_lastDistanceValue != old_distance) {  //If sensor 1 (garage door) distance changed update Blynk
        Blynk.virtualWrite(BLYNK_PIN_DIST, door1_lastDistanceValue);
        old_distance = door1_lastDistanceValue;        
      }
      if(door_status != old_door_status) {  //If sensor 1 (garage door) status changed update Blynk
        if(door_status==1) {
          blynk_door.on();
        } else {
          blynk_door.off(); 
        }
        old_door_status = door_status;
      }
      if(vehicle_status != old_vehicle_status) {  //If sensor 2 (car) status changed update Blynk
        if(vehicle_status==1) {
          blynk_car.on();
        } else {
          blynk_car.off(); 
        }
        old_vehicle_status = vehicle_status;
      }   
      if(old_ip != get_ip()) {  //If IP address has changed update Blynk
        Blynk.virtualWrite(BLYNK_PIN_IP, get_ip());
        old_ip = get_ip();
      }

    }
  #endif
  
}

//Publish a topic to MQTT server
void Publish(char* topic, char* message) { 
  client.publish(topic, message, true);
   
  //Print what was sent to console
  Serial.println(F(""));
  Serial.print(F("Published ["));
  Serial.print(topic);
  Serial.print(F("] "));
  Serial.println(message);
}

/********************************** START RELAY *****************************************/
void toggleRelay(int pin) {
    digitalWrite(pin, RELAYACTIVE);  // turn on relay  
    delay(RELAY_ACTIVE_TIMEOUT);
    digitalWrite(pin, RELAYINACTIVE);  // turn off relay 
}
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
void loop() {

  if (!client.connected()) {
    reconnect();
  }

  unsigned long currentTime = millis();
  
  if (WiFi.status() != WL_CONNECTED) {
    delay(1);
    Serial.print(F("WIFI Disconnected. Attempting reconnection."));
    setup_wifi();
    return;
  }

  client.loop(); // Check MQTT

  ArduinoOTA.handle(); // Check OTA Firmware Updates

  server.handleClient(); // Check Web page requests

  #if BLYNK_ENABLED == true
    if(curr_cloud_access_en()) {
    reconnectBlynk();  //Check if Blynk connected
    }
    
    if(Blynk.connected()) { 
      timer.run();  //timer which runs a periodic Blynk connection check 
      Blynk.run();  //check in with the Blynk server for updates
      blynkup = "yes";       
    }
  #endif

  check_door_status(); // Check the sensors and publish any changes
  
  getESPdata(); // Gather ESP8266 data and publish to MQTT 
  
  #if DHT_ENABLED == true  //Read DHT sensor periodically and publish results to MQTT
    if (currentTime - dht_lastReadTime > (dht_publish_interval_s * 1000)) {
      dht_read_publish();
      dht_lastReadTime = millis();
    }
  #endif

  if (!Blynk.connected()) { 
    //delay(500); // We have enabled Light sleep so this delay should reduce the power used
    delay(800); // We have enabled Light sleep so this delay should reduce the power used
    //delay(2000); // We have enabled Light sleep so this delay should reduce the power used
    //Serial.print(".");      
  }
  
}

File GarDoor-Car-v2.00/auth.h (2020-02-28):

/* Add your keys & customise your settings in this file */

#ifndef _AUTH_DETAILS
#define _AUTH_DETAILS

// Wifi Settings
#define WIFI_HOSTNAME "GarDoor"
#define WIFI_SSID "ssid"
#define WIFI_PASSWORD "password"

// MQTT Settings
#define MQTT_SERVER "mqtt server ip"
#define MQTT_USER ""
#define MQTT_PASSWORD ""
#define MQTT_PORT 1883
#define MQTT_AVAIL_TOPIC WIFI_HOSTNAME "/availability"
#define TimeReadSYS 100000 // time between system readings and MQTT publishing of ESP8266 data
#define topicESPtoMQTT WIFI_HOSTNAME "/ESPtoMQTT"

// OTA Settings for pushing updated software
#define OTApassword "ota password" //the password you will need to enter to upload remotely via the ArduinoIDE
#define OTAport 8266

// Blynk App Settings
#define BLYNK_ENABLED true  //choose to use Blynk app (scan the QR code for OpenGarage project for Blynk App) to monitor/control garage door
#define BlynkAuthToken "enter Blynk token here"
#define BLYNK_NOTIFY true   //choose to be notified in Blynk app when garage door is opened or closed and when garage door is left open for at least 15 minutes 
#define BLYNK_DEFAULT_DOMAIN "blynk-cloud.com"  //Change only if you use a custom Blynk server - public domain name or IP address of your custom server 
#define BLYNK_DEFAULT_PORT 80   // Change only if you use a custom Blynk server - public port of your custom Blynk server
#define BLYNK__AVAIL_TOPIC WIFI_HOSTNAME "/blynkavailability" // MQTT topic to notify if Blynk connected or disconnected

// Distance Parameters
#define ULTRASONIC_MAX_DISTANCE 400 // Maximum distance (in cm) to ping.
#define ULTRASONIC_DIST_MAX_CLOSE 160 // Maximum distance to indicate door is closed (in cm) - Used by sensor 1
#define ULTRASONIC_DIST_MAX_CAR 160 // Maximum distance to indicate car is present (in cm) - Used by sensor 2
#define ULTRASONIC_SETTLE_TIMEOUT 500 // ms to wait between pings (as all sensors get triggered at the same time)
#define RELAY_ACTIVE_TIMEOUT 500 // ms the time the relay will close to actuate the door opener
#define RELAY_ACTIVE_TYPE HIGH   // The digitalwrite to turn on the relay can be HIGH or LOW. If your relay uses LOW as active, enter LOW. If your relay instead uses HIGH as active, enter HIGH.    
#define DOOR_TRIG_PIN 14 // D5 on ESP8266

// Door 1 Parameters (Sensor 1)
#define DOOR1_ALIAS "Door"  //Name to use in MQTT topic and webpage
#define MQTT_DOOR1_ACTION_TOPIC WIFI_HOSTNAME "/1/action"
#define MQTT_DOOR1_STATUS_TOPIC WIFI_HOSTNAME "/1/status"
#define DOOR1_RELAY_PIN 12 // D6 on ESP8266
#define DOOR1_ECHO_PIN 4 // D2 on ESP8266
#define DOOR1_LIMIT_RELAY_CLOSE false  //Do not use the relay to open the door if true (which limits you to closing the door only)

// Car Parameters (Sensor 2)
#define CAR_ALIAS "Car"  //Name to use in MQTT topic and webpage
#define MQTT_CAR_STATUS_TOPIC WIFI_HOSTNAME "/2/status"
#define DOOR2_ECHO_PIN 5 // D1 on ESP8266

// DHT Parameters
#define DHT_ENABLED true
#define DHT_PIN 13 // D7 on ESP8266
#define DHT_TYPE DHT22 // or: DHT21 or DHT22
#define MQTT_TEMPERATURE_TOPIC WIFI_HOSTNAME "/temperature"
#define MQTT_HUMIDITY_TOPIC WIFI_HOSTNAME "/humidity"
#define DHT_PUBLISH_INTERVAL 300  // Number of seconds between each temperature/humidity reading and publish to MQTT 
#define DHT_TEMPERATURE_CELSIUS true  //Use celsius (true) or fahrenheit (false)
#define DHT_TEMPERATURE_ALIAS "Garage Temperature"  
#define DHT_HUMIDITY_ALIAS "Garage Humidity"

#endif
